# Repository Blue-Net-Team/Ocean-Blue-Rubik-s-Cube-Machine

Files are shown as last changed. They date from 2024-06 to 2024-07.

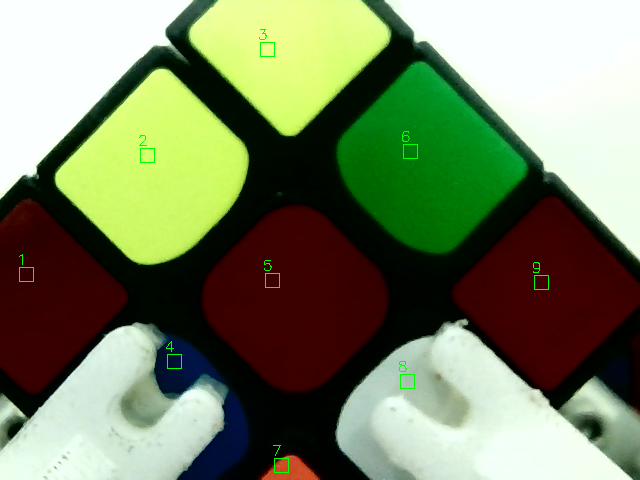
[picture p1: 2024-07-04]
Vision/pic/L/L.png

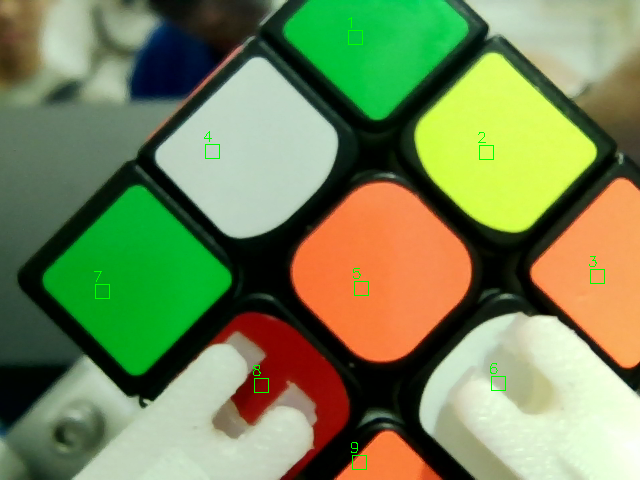
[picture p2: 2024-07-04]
Vision/pic/R/Rt.png

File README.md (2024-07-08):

# 海蓝魔方机

针对2024年的[中国高校智能机器人创意大赛](https://www.robotcontest.cn/datacenter/news/detail?id=6292)的主题2，还原魔方的机器人，追求更快的速度。

**本项目为2024年中国高校智能机器人创意大赛的参赛作品，仅供学习交流使用，不得用于商业用途。**

## 开发团队

- 院校：广东海洋大学
- 所属学院：机械工程学院
- 团队名称：[蓝网科技创新团队](https://gitee.com/blue-net-vision)
- 队伍成员：
  - 视觉：[许凯杰](https://gitee.com/d-vision)，[何云峰](https://gitee.com/iven_he)
  - 算法：[许凯杰](https://gitee.com/d-vision)
  - 电控：[何云峰](https://gitee.com/iven_he)
  - 结构：吉泧均，何云峰

## 开发平台

- NVIDIA jetson nano
- ESP32-S3R8N8

## 开发环境

- 操作系统：Ubuntu
- 开发语言：Python

## 参考

1. [SVM识别方案](https://blog.csdn.net/lemonbit/article/details/117004167)
2. [魔方解算算法](https://github.com/hkociemba/RubiksCube-TwophaseSolver)
3. [机械臂规划算法](https://gitee.com/harry-fan/rubiks-cube-robot)

## 介绍

本魔方机器人采用双爪八字布局，4个摄像头，两个步进电机，气滑环，以及夹爪气缸。通过空压机给气罐充气，撤除空压机，将魔方夹稳，按下启动按钮，夹爪闭合，开始还原魔方。

### 设备清单

- NVIDIA jetson nano
- [ESP32-S3R8N8](https://item.szlcsc.com/22034693.html?fromZone=s)
- 4个摄像头
- [42步进电机-L40](https://item.taobao.com/item.htm?id=682797640293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) + [闭环控制器Emm42工业版](https://item.taobao.com/item.htm?id=673302946671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) *2
- [MHL2-16D夹爪气缸](https://item.taobao.com/item.htm?id=537049565191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) *2
- [气滑环 2路气 侧边出气M5牙](https://detail.tmall.com/item.htm?_u=d2qf50kdb8b2&id=555594152568&skuId=3431370232744)*2
- [二路五通电磁阀](https://item.taobao.com/item.htm?spm=a1z09.2.0.0.2e4a2e8dQz8SzG&id=631999517519&_u=42qf50kd72cc)*2
- [200M 2F汇流排](https://item.taobao.com/item.htm?spm=a1z09.2.0.0.2e4a2e8dQz8SzG&id=682537654244&_u=42qf50kd02df)
- [200M堵头3个和消音器2只](https://item.taobao.com/item.htm?spm=a1z09.2.0.0.2e4a2e8dQz8SzG&id=682537654244&_u=42qf50kd02df)
- [12v锂电池](https://item.taobao.com/item.htm?spm=a1z09.2.0.0.2e4a2e8dQz8SzG&id=632184698346&_u=42qf50kd578b)
- 若干 6mm气管连接头

## 说明

作为上位机的jetson nano会使用svm识别魔方的各色块颜色，得出魔方当前姿态，然后使用魔方解算算法得出还原步骤，但是还原步骤并不能直接传给下位机操控两个机械臂，要对还原步骤进行最短路径计算，得出最短的机械步骤，将机械步骤发送给下位机的ESP32，ESP32会控制步进电机和气缸，完成魔方的还原。\
此机器框架使用30铝型材，全金属框架，**电路板需要注意防止短路**

### 使用说明

本项目主要使用难点在于视觉方面，一下回主要介绍Jetson nano的连接和程序启动，调试等部分

#### 连接

首先将jetson nano开机，使用vscode的远程连接功能连接Jetson nano。对于首次使用Jetson nano，需要使用外接显示屏来连接WiFi，确认IP地址等操作。此后的连接方式与树莓派一致。

#### 魔方摆放

此视觉识别方案中，对魔方的摆放有具体要求，因为需要将识别到的颜色映射成魔方每个面，才能进行解算，所以魔方中心
块的颜色就对应这个面，如Blue->U，这在字典中已经被绑定。

摄像头的示例图片位于路径 **./Vision/pic** 中，摄像头对应的识别文件 **./Vision/cam** 中。\
在图片中，上侧摄像头的左侧就是左机械臂所在一侧，以此一来：

- **蓝色面**在右手机械臂的上方
- **橙色面**位于机器前方(右摄像头正对位置)，即人面向机器时左手对应左机械臂时人所在机器的位置
- 以此类推

#### ROI区域调试

本项目使用vscode进行调试，不依赖外部显示器，所以不能在代码中使用OpenCV有关qt窗口的函数，为了解决快速调试的需求，我们使用远程图传用于调试ROI区域。

- 我们在*Vision*文件夹中编写了*ROIlocater.py*文件，用于快速调整摄像头对各个色块的ROI区域\
- 我们在*Vision*文件夹中同样编写了Jetson nano 上运行的远程图传文件*Captest.py*，文件的运行需要使用命令行传参，使用*Python Debugger*进行调试的时候需要选择**带有参数的Python文件**，在交互框中协商对应的参数名和参数\
`--cap 1` 此参数的意义是使用摄像头id为`1`的摄像头进行远程图传。\
或者直接在命令行直接用Python命令运行Python文件

  ```bash
  python Captest.py --cap 1
  ```

启动*ROIlocater.py*文件前需要修改222行的参数`serface_name`，改为需要修改的对应的摄像头的位置，例如

- 上摄像头：U
- 下摄像头：D
- 左摄像头：L
- 右摄像头：R

**先启动Jetson nano上的远程图传服务器程序，再启动对端的*ROIlocater.py*文件**

两个文件都启动后会弹出滑块窗口用于调整滑块的位置、大小和编号。调整前需要查看事例图片上的编号顺序，ROI的顺序不能出错。ROI的编号对应的是滑块*ID*的值，**ID为0的时候是无效ROI**

示例图片位于文件夹 **./Vision/pic** 中。

对应示例的图片**随机应变**，按照ROI顺序依次点击识别区域，此操作尽可能需要在步进电机通电的情况进行，这样可以保证电机的角度基本不变。使用鼠标单击完成ROI设置后就可以直接结束程序。在滑块窗口中有*OK*标签的滑块充当保存按钮，使用鼠标单击的模式可以直接忽略这个滑块，但是如果是使用滑块来调节ROI位置的需要将*OK*标签滑到1进行保存在回到0复位。

完成ROI设置后，将工作目录中的对应json文件复制到Jetson nano 的工作目录中，替换原有的json文件就可以完成ROI的设置。

#### 识别调试

在本项目中，调整好ROI区域后大部分报错是由颜色识别出错导致，运行*main.py*文件可以直接查看各个摄像头的识别结果，识别的图片会保存在 **./Vision/pic** 文件夹下以摄像头位置命名。依据图片和结果一一对比，查出识别出错的摄像头，在对应的摄像头文件中(位于文件夹 **./Vision/cam** 中)修改亮度,大部分是识别问题都可以通过修改亮度来解决。

```python
# 自动曝光
cap.set(cv2.CAP_PROP_AUTO_EXPOSURE, 3)

cap.set(10,0) # 亮度0
```

经过测试，自动曝光参数`3`效果最佳

## 开发说明

- **Vision**文件夹用于存储视觉识别以及魔方解算的代码
- **Control**文件夹用于存储电控代码，是一个microPython工程文件夹，在*vscode*中安装*RT-Thread MicroPython*插件，在此文件夹创建microPython工程，即可连接到ESP32，进行代码编写，但是请确保esp32的固件已经烧录
  - 在[microPython官网](https://micropython.org/)下载esp32的固件
  - 使用esptool或者[Thonny](https://micropython.org/)烧录固件
- **Structure**文件夹用于存储机械结构相关模型，使用*SolidWorks2023*打开
- **PCB**文件夹用于存储电路板设计文件，使用*嘉立创EDA专业版*打开

# 最后说明

此仓库中的Raspberry Pi分支是原来只使用树莓派进行开发的版本，现在已经废弃，不再维护，如果有相关需求或者想法可以加入我们。

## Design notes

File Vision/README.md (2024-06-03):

# 视觉上位机

此文件夹是用于存放视觉识别和魔方姿态解算的上位机程序，主要用于调试和测试视觉识别和魔方姿态解算的算法。

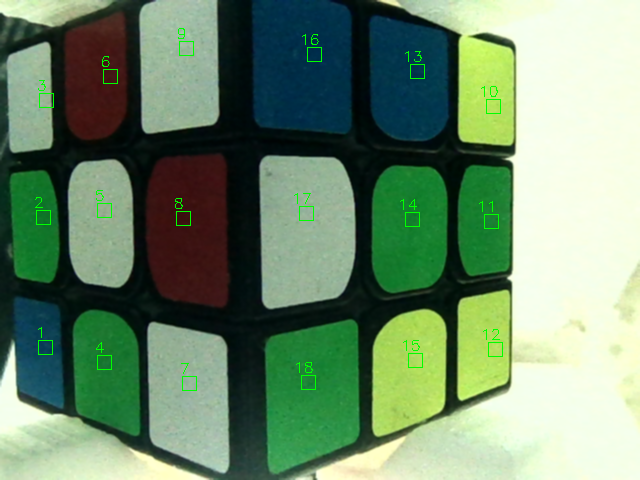
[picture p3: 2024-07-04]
Vision/pic/D/Dt.png

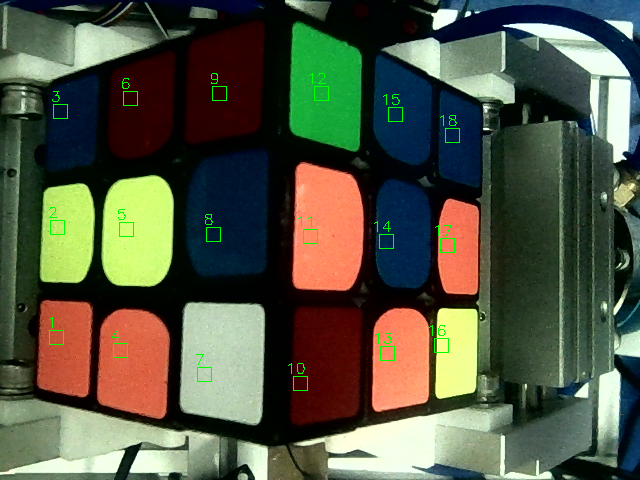
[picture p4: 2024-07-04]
Vision/pic/U/Ut.png

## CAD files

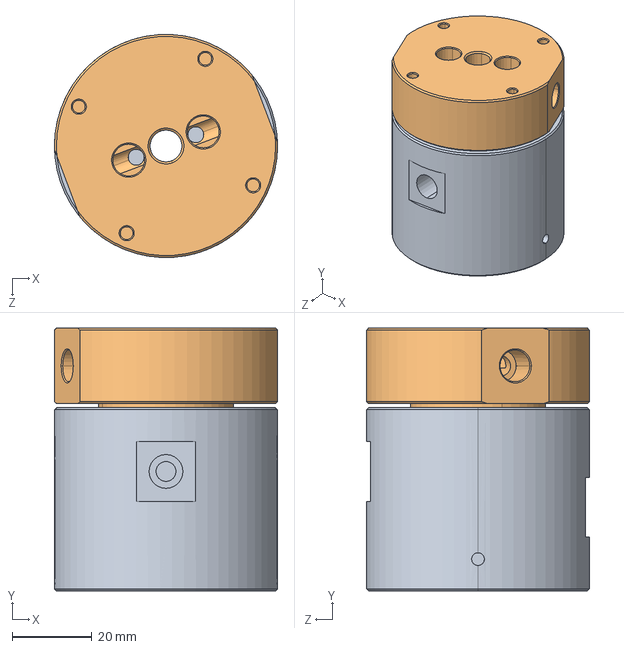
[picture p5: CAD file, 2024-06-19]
Structure/气滑环.SLDASM
56.0 x 66.0 x 56.0 mm
气滑环上
气滑环下

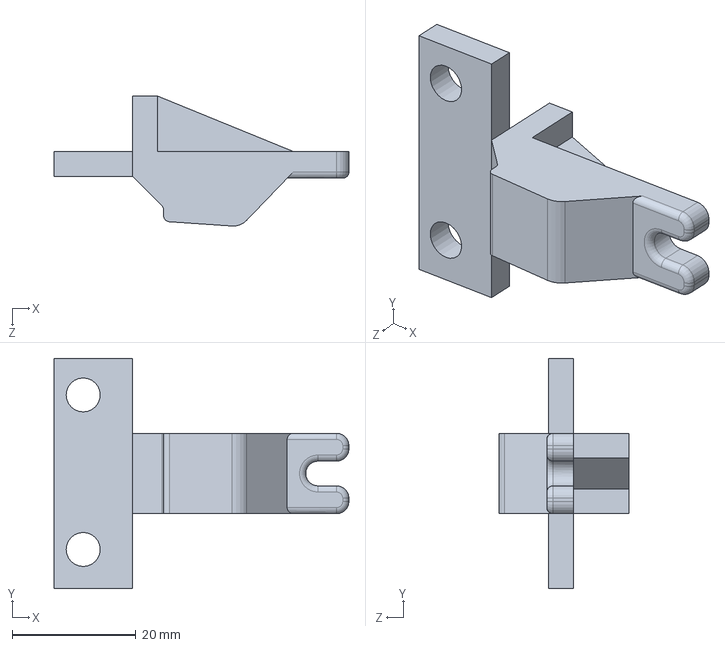
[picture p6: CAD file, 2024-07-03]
Structure/手指.SLDPRT
47.7 x 37.3 x 21.0 mm

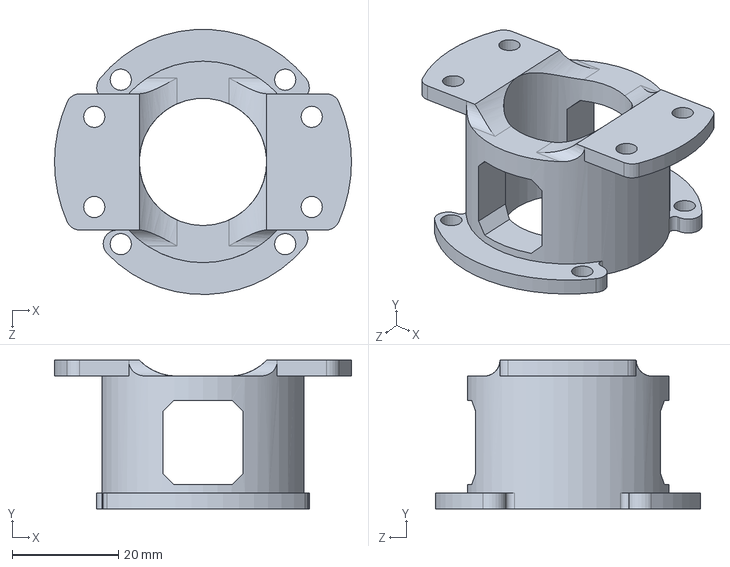
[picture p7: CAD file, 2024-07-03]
Structure/电机-气滑环连接盘.SLDPRT
56.0 x 28.0 x 49.9 mm

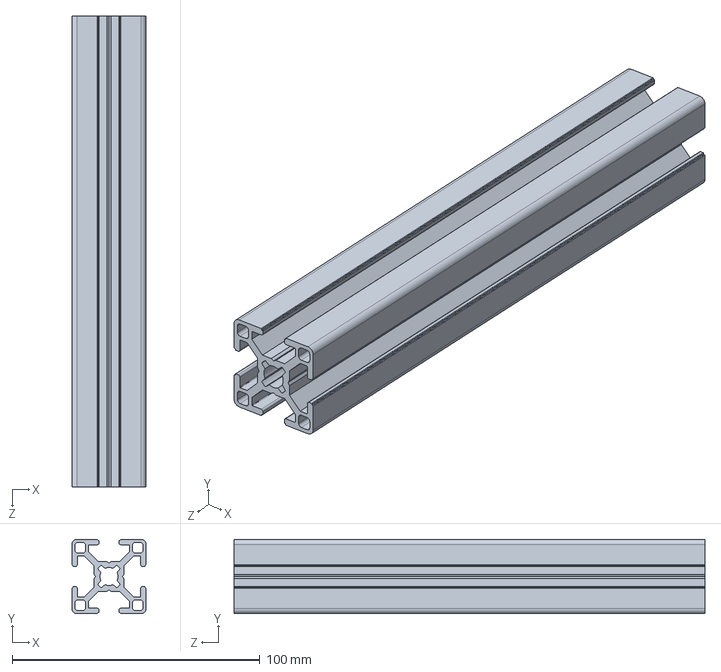
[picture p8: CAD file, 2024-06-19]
Structure/30×30×190.SLDPRT
30.0 x 30.0 x 190.0 mm

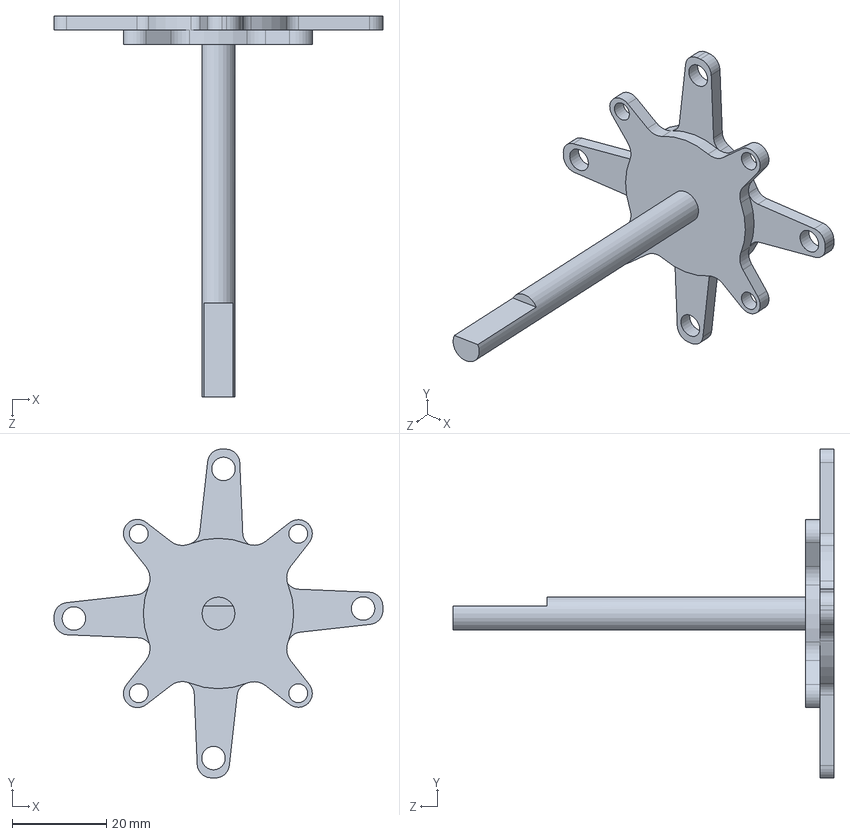
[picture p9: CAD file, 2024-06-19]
Structure/传动轴 - 2024.SLDPRT
70.0 x 70.0 x 81.0 mm

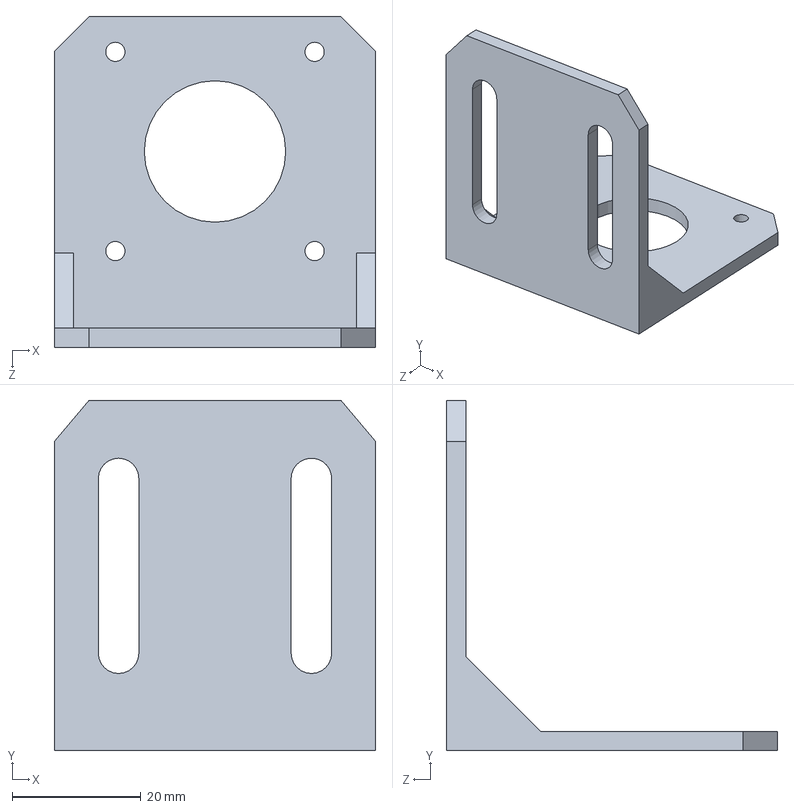
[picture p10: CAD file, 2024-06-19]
Structure/42步进电机支架.SLDPRT
50.0 x 54.5 x 51.5 mm

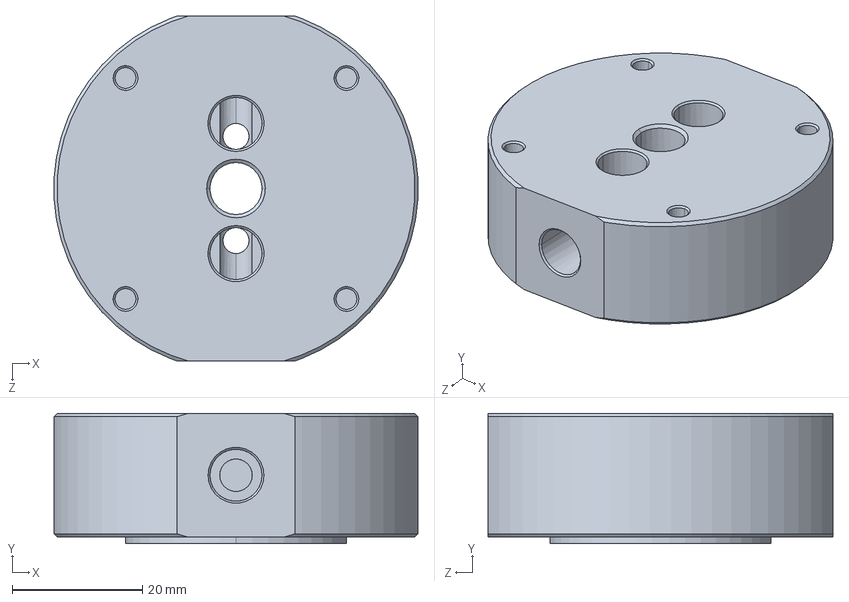
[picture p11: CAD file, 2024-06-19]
Structure/气滑环上.SLDPRT
55.9 x 20.0 x 53.0 mm

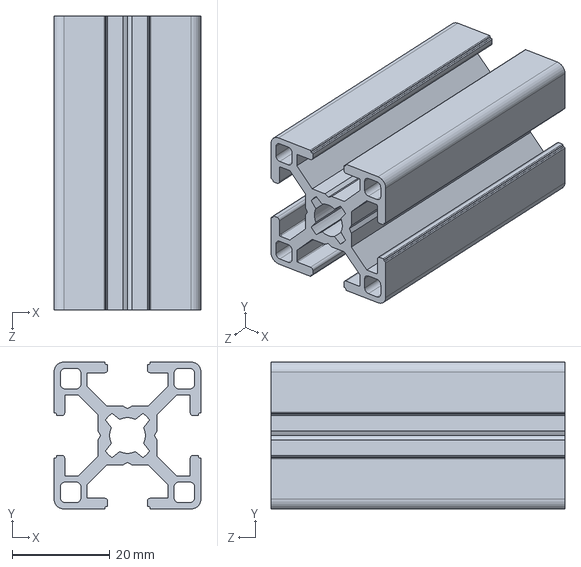
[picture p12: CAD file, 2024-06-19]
Structure/30×30×60.SLDPRT
30.0 x 30.0 x 60.0 mm

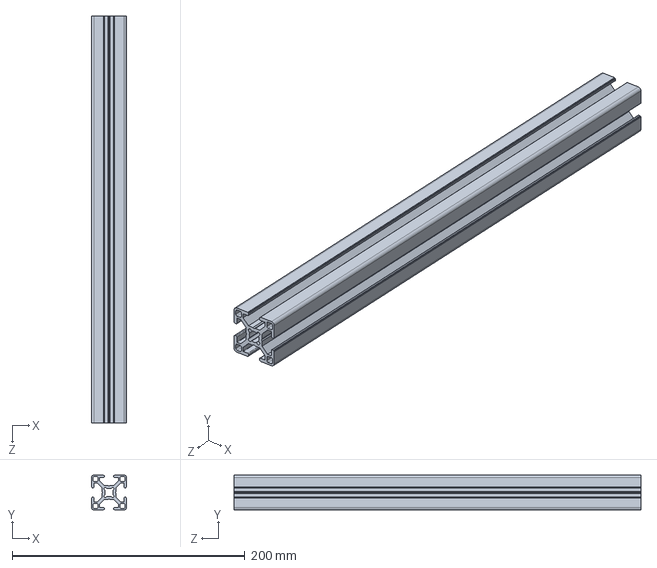
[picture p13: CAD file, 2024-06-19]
Structure/30×30×350.SLDPRT
30.0 x 30.0 x 350.0 mm

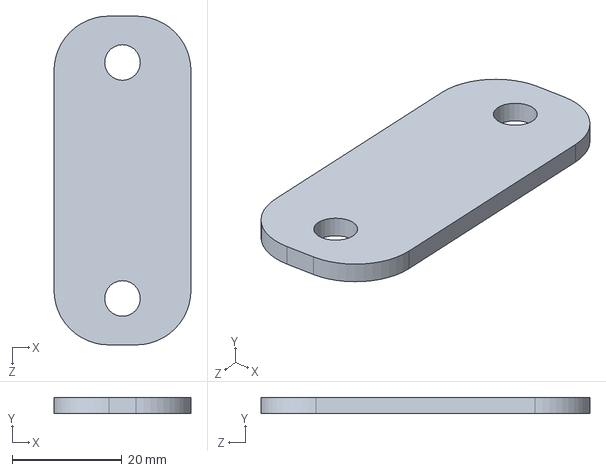
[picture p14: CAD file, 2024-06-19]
Structure/铝型材连接板.SLDPRT
25.0 x 3.00 x 60.0 mm

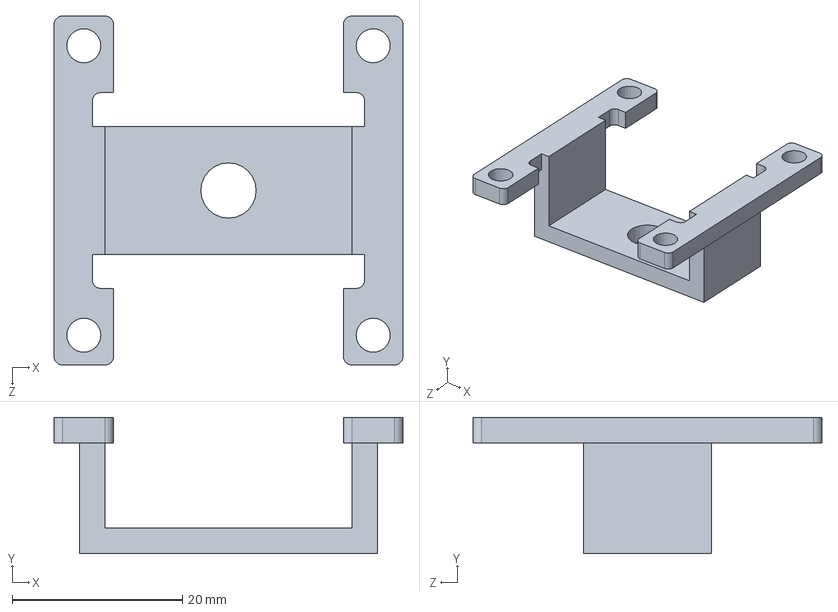
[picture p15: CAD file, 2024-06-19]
Structure/摄像头连接架.SLDPRT
41.0 x 16.0 x 41.0 mm

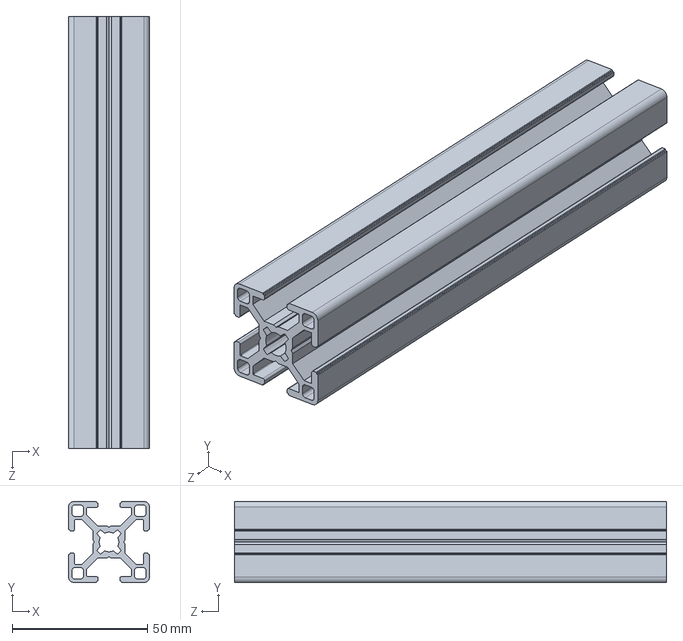
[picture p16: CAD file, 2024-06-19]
Structure/30×30×160.SLDPRT
30.0 x 30.0 x 160.0 mm

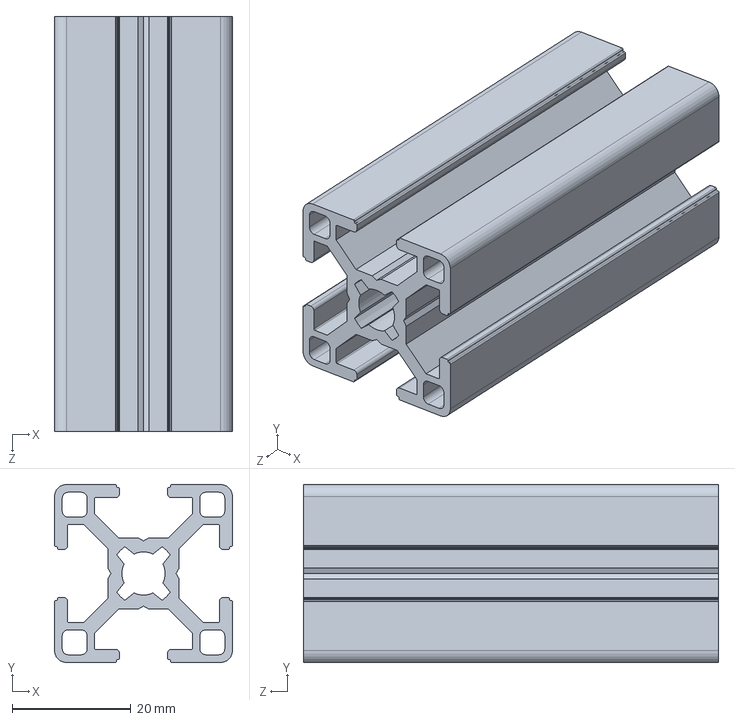
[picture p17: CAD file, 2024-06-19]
Structure/30×30×70.SLDPRT
30.0 x 30.0 x 70.0 mm

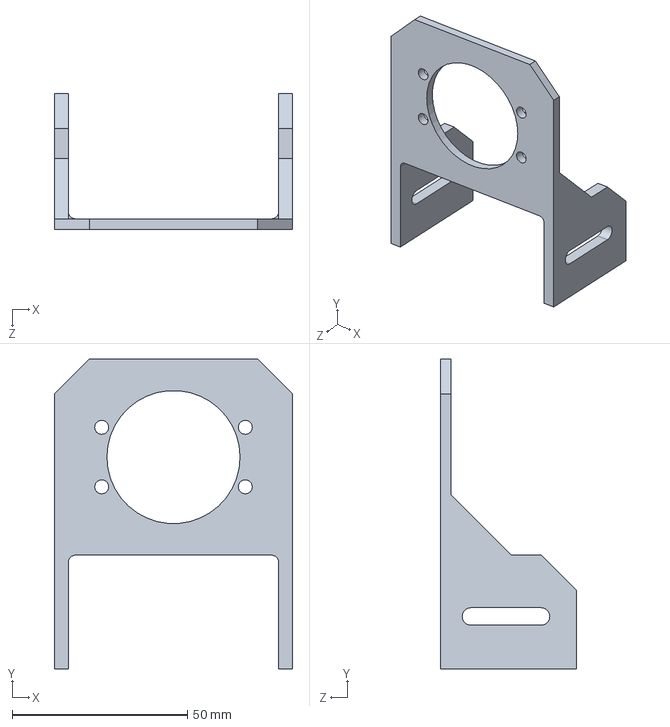
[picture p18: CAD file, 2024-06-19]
Structure/气滑环铝架固定.SLDPRT
68.0 x 88.5 x 38.7 mm

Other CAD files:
Structure/电机.SLDASM
Structure/气滑环固定铝框架(145改).SLDASM
Structure/RubiksCube.SLDASM
Structure/气滑环下.SLDPRT
Structure/30-30铝型材连接件.SLDPRT
Structure/30×30×205.SLDPRT
Structure/30×30×265.SLDPRT
Structure/夹爪.SLDPRT
Structure/摄像头.SLDPRT
Structure/铜柱.SLDPRT

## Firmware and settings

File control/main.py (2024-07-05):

r"""
*********************************************
                   _ooOoo_
                  o8888888o
                  88" . "88
                  (| -_- |)
                  O\  =  /O
               ____/`---'\____
             .'  \\|     |//  `.
            /  \\|||  :  |||//  \
           /  _||||| -:- |||||-  \
           |   | \\\  -  /// |   |
           | \_|  ''\---/''  |   |
           \  .-\__  `-`  ___/-. /
         ___`. .'  /--.--\  `. . __
      ."" '&lt;  `.___\_&lt;|>_/___.'  >'"".
     | | :  `- \`.;`\ _ /`;.`/ - ` : | |
     \  \ `-.   \_ __\ /__ _/   .-` /  /
======`-.____`-.___\_____/___.-`____.-'======
                   `=---='

			   佛祖镇楼 永无BUG
^^^^^^^^^^^^^^^^^^^^^^^^^^^^^^^^^^^^^^^^^^^^^
"""
import time
from machine import Pin, UART
from machine import I2C
import ssd1306
from arm import SteppingMotor, ClampCylinder


def restore():
    """还原
    ----
    收到信号触发"""
    for index, now_step in enumerate(str_data_lst):
        if len(now_step) != 2:      # 确认步骤合法
            oled.fill(0)
            oled.text("Invalid step", 0, 0)
            oled.show()
            print("Invalid step")
            return
        oled.fill(0)                        # 清屏
        oled.text(f'{now_step}', 0, 10)     # 显示当前步骤
        oled.show()                         # 显示

        sign1 = now_step[0]        # L or R
        sign2 = now_step[1]        # ["1", "2", "3", "O", "C"]
        
        # 确认下一步
        try:
            next1_step = str_data_lst[index+1]
            try:
                next2_step = str_data_lst[index+2]
            except IndexError:
                next2_step = [None, None]
        except IndexError:
            next1_step = [None, None]

        # 调整延迟
        if next1_step[0]!=sign1:     # 下一步在不同手臂
            # t1:手指张和后的延迟
            # t2:手腕旋转后的延迟
            t1=0.1
            t2=0.2
            if next1_step[1] in ['1', '2', '3'] and now_step[1] in ['O']:        # [LO,R1,LC]
                t1=0.07
            if now_step[1] in ['1', '2', '3'] and next1_step[1] in ['C']:
                t2=0.24
        else:
            t1=0.13
            t2=0.23
        
        # 确认左右手
        if sign1 == "L":
            motor = left_motor
            cylinder = left_cylinder
            _cylinder = right_cylinder
        elif sign1 == "R":
            motor = right_motor
            cylinder = right_cylinder
            _cylinder = left_cylinder
        else:
            oled.fill(0)
            oled.text("Invalid step", 0, 0)
            oled.show()
            print("Invalid step")
            return

        # 选择动作
        if sign2 == 'O' and index == len(str_data_lst)-3:                # 这一步是张手指并且是倒数第三步
            if next1_step[0] == sign1:      # 下一步在同一手臂
                if next1_step[1] in ['1','3'] and next2_step[1] in ['C']:
                    _cylinder.open()
                    time.sleep(0.05)
                    motor.rotate('1', 0)
                    cylinder.open()
                    break
        elif sign2 in ["O", "C"]:
            if sign2 == 'O':
                cylinder.open()
            if sign2 == "C":
                cylinder.close()
            time.sleep(t1)
        elif sign2 in ['1','2','3']:
            if sign2 in ["1", "3"]:
                motor.rotate(sign2, 0)
            elif sign2 == "2":
                motor.rotate(sign2, 0)
            time.sleep(t2)
        else:
            oled.fill(0)
            oled.text("Invalid step", 0, 0)
            oled.show()
            print("Invalid step")
            return
        

def read(ser:UART, HEAD:str='@', TAIL:str='#') -> bytes:
    PACKET_HEAD = HEAD.encode('ASCII')
    PACKET_TAIL = TAIL.encode('ASCII')

    data = b''  # 用于存储接收到的数据

    while True:
        byte = ser.read(1)
        if byte == b'' or byte is None:
            continue
        if byte == PACKET_HEAD:
            data = b''
            continue
        if byte == PACKET_TAIL:
            break
        data += byte
    return data

if __name__ == "__main__":
    # region 创建对象
    left_cylinder = ClampCylinder(11)
    right_cylinder = ClampCylinder(12)
    print("Cylinder created")

    gas_switch = Pin(41, Pin.OUT)
    print("Gas switch created")

    led = Pin(9, Pin.OUT)
    print("LED created")

    IIC = I2C(0, scl=Pin(5), sda=Pin(4))
    print("IIC created")

    oled_width = 128
    oled_height = 64
    oled = ssd1306.SSD1306_I2C(oled_width, oled_height, IIC)
    print("OLED created")
    # endregion 

    while True:
        # 与Jetson Nano通信的串口对象
        uart = UART(1, baudrate=9600, tx=8, rx=7)       # type: ignore
        # region 读取数据
        data = read(uart)
        str_data = data.decode()
        str_data_lst = str_data.split(' ')
        # endregion
        # print(str_data_lst)
        del uart
        print('uart release')

        left_motor = SteppingMotor(stp=47, en=48, _dir=38)
        right_motor = SteppingMotor(stp=40, en=39, _dir=21)
        print("Motor created")

        print(str_data_lst)

        t0 = time.time()        # 计时开始
        oled.fill(0)            # 清屏

        gas_switch.value(1)     # 打开气源
        oled.text(f'{len(str_data_lst)} steps', 0, 0)
        led.on()        # 就绪指示灯亮起
        restore()       # 还原
        led.off()       # 就绪指示灯熄灭

        t1 = time.time()        # 计时结束
        oled.fill(0)            # 清屏
        oled.text(f'Finish in', 0, 0)        # 显示时间
        oled.text(f'{t1-t0}', 0, 10)
        oled.text(f'seconds', 0, 20)
        oled.show()        # 刷新屏幕

        # 打开两个手指
        left_cylinder.open()
        right_cylinder.open()

        # 关闭气源
        gas_switch.value(0)

        time.sleep(10)       # 等待1s

        # 关闭两个手指
        left_cylinder.close()
        right_cylinder.close()

        del left_motor
        del right_motor
        print("Motor release")

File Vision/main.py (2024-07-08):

import cube_solver
import time
import communication
import arm_planning
import cam
import cv2
from multiprocessing import Pool

Ucam = cam.UpCam()
Dcam = cam.DownCam()
Lcam = cam.LeftCam()
Rcam = cam.RightCam()

ifio:bool=True

def main_detect_color(img:cv2.typing.MatLike, _cam:cam.Cam):
    return _cam.detect_color(img, ifio)
    
def main_read_img(side:str):
    if side == 'U':
        return Ucam.read_usb_capture()
    elif side == 'D':
        return Dcam.read_usb_capture()
    elif side == 'L':
        return Lcam.read_usb_capture()
    elif side == 'R':
        return Rcam.read_usb_capture()
    else:
        raise ValueError("side must be in ['U','D','L','R']")

def crack():
    t1 = time.perf_counter()
    # 获取魔方颜色状态
    with Pool(4) as p:
        img_res = p.map(main_read_img,['U','R','L','D'])
    t2 = time.perf_counter()
    print(f'read time {t2-t1}')

    res0 = [
            main_detect_color(img_res[0],Ucam),
            main_detect_color(img_res[1],Rcam),
            main_detect_color(img_res[2],Lcam),
            main_detect_color(img_res[3],Dcam)
            ]
    t2 = time.perf_counter()
    print('detect time:',t2-t1)

    color_state2,color_state3 = res0[0]     # type:ignore
    color_state1 = res0[1]
    color_state4 = res0[2]
    color_state5,color_state6 = res0[3]     # type:ignore
    color_state = color_state3 + color_state1 + color_state2 + color_state6 + color_state4 + color_state5   # type:ignore
    color_state = cube_solver.color2view(color_state)
    print("color state is:" + color_state)

    # 解算得到机械臂步骤
    solve_step = cube_solver.cube_solver(color_state)
    _solve_step = solve_step.split()
    _solve_step = _solve_step[:-1]
    print("the orign step is:", _solve_step)
    real_solve, cost = cube_solver._SolutionTransAndOptimize(_solve_step)
    # real_solve = _solve_step
    arm_step = arm_planning.planning(real_solve)  # ['RO', 'L2', 'RC', 'R2']
    print("--------------------------------------------")
    print("the optimize step is:",real_solve)
    print("--------------------------------------------")
    print("arm_step:",arm_step)
    
    step_str = ' '.join(arm_step)

    Transmitter.write(step_str)
    
    return arm_step

Transmitter = communication.UART()

if __name__ == '__main__':
    input("Press 'enter' to continues:")
    crack()

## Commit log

2024-02-18 初始更改
2024-02-19 更改英文readme
2024-02-19 还原中文readme
2024-02-20 完善队伍成员
2024-03-05 在控制魔方转动的文件中添加了对步进电机控制的方法
2024-03-05 添加了对魔方六面结构的定义
2024-03-06 将GPIO模式放在全局位置
2024-03-06 添加夹爪气缸类
2024-03-07 添加测试
2024-03-07 添加对于使能引脚的必须
2024-03-07 将角度更改为圈数，并且可以稳定运行
2024-03-07 新建 vision
2024-03-07 删除文件 vision/.keep
2024-03-07 删除文件 vision/vision/.keep
2024-03-07 新建 model
2024-03-07 删除文件 vision/model/.keep
2024-03-07 重命名 vision 为 vision(电科版)
2024-03-07 提高了脉冲速度
2024-03-07 update vision(电科版)/README.md.
2024-03-08 重命名 vision(电科版) 为 Vision
2024-03-09 专注于电控控制，算法移交给徐凯杰
2024-03-09 更改注释
2024-03-10 解决了步进电机转动慢的问题
2024-03-10 进一步提高步进电机转速
2024-03-13 添加文件注释和函数注释
2024-03-13 删除无关文件
2024-03-13 更新readme
2024-03-13 更新依赖
2024-03-16 添加机械臂的类
2024-03-16 添加魔方公式解算器的右侧空转的方法，并且改进了变量的类型解释
2024-03-16 添加空转函数返回值和注释
2024-03-16 添加左侧空转的方法
2024-03-16 补充机械臂的手指闭合的方法
2024-03-16 手指归为的方法补充手指闭合
2024-03-16 添加右侧旋转魔方的方法
2024-03-16 添加左侧旋转魔方的方法
2024-03-20 添加手指闭合和旋转的机械臂成员
2024-03-27 Add steeringEngine class for controlling the steering angle
2024-05-12 编写了在ESP32内运行的代码
2024-06-01 重构电机转动逻辑并添加UART通信
2024-06-01 重构control.py以提高代码可读性和错误处理
2024-06-02 重命名 Vision 为 Flash
2024-06-03 重命名 Flash/vision/color_detect_use1.py 为 Flash/vision/Right.py
2024-06-03 重命名 Flash/vision/color_detect_use2.py 为 Flash/vision/Up.py
2024-06-03 重命名 Flash/vision/color_detect_use4.py 为 Flash/vision/Down.py
2024-06-03 重命名 Flash/vision/color_detect_use3.py 为 Flash/vision/Left.py
2024-06-03 删除多余代码
2024-06-03 添加注释
2024-06-03 添加特殊注释
2024-06-03 将vision文件夹重命名为cam
2024-06-03 将Flash文件夹重命名为Vision
2024-06-03 取消了未使用的代码块
2024-06-03 修复串口通信问题
2024-06-03 将空格分隔的串口数据转成列表
2024-06-03 需要修复的问题
2024-06-04 修改路径及模块名
2024-06-04 更新了串口发送的逻辑
2024-06-06 重构旋转方法以接受符号参数
2024-06-07 删除注释
2024-06-11 更新ignore
2024-06-11 重命名并且更改位置
2024-06-11 解决了串口无法接受不确定长度信息的问题
2024-06-11 将串口器放入全局，完善调用
2024-06-13 更新ROI及摄像头参数
2024-06-13 重构代码，使外部中断只能发送一次数据，接收到步骤后立即开始还原
2024-06-13 添加PCB和原理图源文件
2024-06-13 更新神奇算法
2024-06-13 更新注释
2024-06-14 测试案例
2024-06-15 此提交需要使机器在5个大气压以上的气罐环境下运行，可以使机器完成一个完整的还原动作
2024-06-15 添加ROI调整文件
2024-06-17 解决串口通信已知问题
2024-06-17 添加fixme
2024-06-17 重命名测试文件
2024-06-17 添加模型文件
    [30-30铝型材连接件.SLDPRT, 30×30×160.SLDPRT, 30×30×190.SLDPRT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]
2024-06-19 重构还原函数，使延迟的调试更轻松；重构代码，使程序保持运行
2024-06-19 添加的OLED相关库
2024-06-19 新添加一个电磁阀用来控制总气体的通断，添加了OLED屏幕显示步骤次数以及当前的步骤
2024-06-19 更新自动标框
2024-06-19 更新自动标注
2024-06-19 注释无法安装的库并且修改函数返回值
2024-06-19 将测试文件添加了转换成机械步骤的方法
2024-06-19 添加qt有关的方法的注释，屏蔽窗口产生，便于vscode远程运行；修改ROI参数
2024-06-20 添加判断条件
2024-06-20 更改路径
2024-06-20 提交了可以快速寻找ROI的方法
2024-06-20 添加了在屏幕上输出还原时间的功能
2024-06-21 删除多余函数
2024-06-21 更新模型文件
    [手指.SLDPRT]
2024-06-21 提取窗口名作为常量
2024-06-21 添加了使用串口控制步进电机的方法
2024-06-21 封装了一个读取串口数据的函数
2024-06-21 将保存函数的path参数提取
2024-06-22 将有关机械臂的相关封装放进主文件之外
2024-06-23 为步进电机类添加UART通信和新方法
2024-06-23 重构代码:组织导入并删除未使用的类和方法
2024-06-23 修复了屏幕上不像是当前步骤的问题
2024-06-29 更新ROI以及摄像头参数
2024-06-29 解决已知问题
2024-07-01 添加了远程图传的类，并且解决了已知问题
2024-07-01 使摄像头的识别可以读取ROI的json文件，并且在画出ROI框的时候标记ROI的序号
2024-07-01 更新主文件的延迟
2024-07-01 解决了ID滑块不能更新的问题
2024-07-03 解决了已知问题，减去传参num_id
2024-07-03 更新模型
    [手指.SLDPRT, 电机-气滑环连接盘.SLDPRT]
2024-07-03 解决了PCB中网络交错导致信号线交叉的问题
2024-07-03 更新main，使最后三步如果识别到是多余步骤直接结束
2024-07-04 添加事例图片
2024-07-04 添加远程图传调试文件
2024-07-04 将main里面的识别加上面的标识，并且使用input来开始程序
2024-07-05 将摄像头封装
2024-07-05 更新cam文件夹
2024-07-05 在main文件使用多进程并发操作，有效提高识别速度
2024-07-05 加长solve函数的timeout，提高步骤质量
2024-07-05 重构cam文件夹下的文件，减少代码量
2024-07-06 更新父类定义
2024-07-06 将摄像在类定义中直接打开，节省了主线程打开摄像头的时间
2024-07-06 主文件中为更改了并发逻辑，将图片传入进程池，解决摄像头不可序列化的问题
2024-07-06 不再使用多进程，识别时间缩短到0.06秒以内
2024-07-06 将t1前移
2024-07-06 使用并发读取摄像头图片，读取时间从1.4秒缩短到0.9秒
2024-07-06 重构代码，减少代码量
2024-07-06 优化sv.solve参数
2024-07-07 魔方摆放解释
2024-07-08 更新英文readme
2024-07-08 使用继承的方式大量简化代码(等待测试)
2024-07-08 简化代码
